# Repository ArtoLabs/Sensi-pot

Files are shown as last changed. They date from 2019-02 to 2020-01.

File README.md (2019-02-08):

#### Sensi-pot is open source hardware and software 
designed to help automate routine indoor garden processes such as lighting cycles, environment control, watering, and nutrient regulation. A prolific boom in the marijuana industry is taking place in Colorado, Oregon, and Washington states in the U.S. (and soon many other states) causing an increased demand for indoor gardening products. Especially in Colorado, where the winter is long and cold, most marijuana is grown indoors; necessitating equipment to help control and mimic the plant's native environment. This is especially needed for growing marijuana, which is very sensitive to heat and humidity (or lack thereof). However, most indoor gardening automation equipment is designed for big production facilities and is usually too expensive for the average grower. Sensi-pot provides electronics kits that can be easily assembled by anyone with a soldering iron, allowing the average user access to the same type of technology available to bigger growers at a fraction of the price.

# Sensi-Pot Indoor Environment Controller

This is the first Sensi-Pot open source automation device made for regulating the temperature and humidity of an enclosed space, including greenhouses. Marijuana grows best when the environment is kept at a perfect balance, and this device can maintain a perfect 55% humidity and 75 degrees fahrenheit, which is perfect for marijuana. The controller can be adjusted to regulate any temperature or level of humidity. At the heart of the device is the custom circuit board, which can be ordered using the open source Gerber files, or by [ordering through PCBway.com](https://www.pcbway.com/project/shareproject/Sensi_pot_Indoor_Environment_Controller.html) (see below for more info).

### Features

* Controls temperature to within 2 degrees.

* Controls humidity to within 5%.

* Wifi webserver shows the current temp and humidity as well as provides a manual way to active/deactivate any of the devices connected to it. You can also pause/unpause data logging from the web page as well as erase all data on the SD card.

* Data logging records the temperature and humidity with a timestamp to an SD card.

* Displays the current time, temperature and humidity on an LCD

### Hardware Specifications

* Designed using the open source PCB design and editing software, Kicad, so any changes you'd like to make to the circuit board can easily be done using the Kicad files available on Github.

* Uses the ATMEGA328P microcontroller, the same that can be found on any Arduino.

* The ATMEGA328P was programmed using the open source Arduino IDE software and uses some of the Arduino libraries in it's C++ code.

* Uses the ESP01 wifi module to serve a basic web page on the local network. To connect to a secured network the code must be modified slightly to include the SSID and the router password. The ATMEGA328P microcontroller communicates with the ESP01 using standard serial communication.

* Can technically control up to 8 devices and simply needs an 8 channel relay to do this. The pictures in this post show the controller connected to a 4 channel relay which is capable of controlling a heater, air conditioner, humidifier and dehumidifier. The other 4 devices can include lights and fans.

* Uses the DHT11 humidity and temperature sensor which can sense temperatures from 0 to 50 degrees Celsius (32 to 122 degrees Fahrenheit) +/- 2 degrees and can sense humidity from 20% to 80% +/- 5%. This can easily be replaced with no additional code with the DHT22 which has a temperature range of -40 to 125 (+/- 0.5) degrees Celsius and a humidity range of 0% to 100% (+/- 2 to 5 percent).

* Uses the MicroSD module to write logging data to any standard micro SD card. The ATMEGA328P communicates with the MicroSD module using the serial peripheral interface (SPI).

* Powered by the LM2596 adjustable buck converter which steps down any voltage between 9 and 34 volts to a regulated 5 volts used by the ATMEGA328P and it's peripheries. The voltage is further stepped down to 3.3 volts by the LM317 linear voltage regulator for use by the ESP01 wifi module. The Environment Controller consumes about 1.5 amps, with a peak current around 2 amps.

* Includes port access to programming pins via a 5 pin header that can be used to program the Environment Controller with an Arduino. Also includes access to the RX and TX pins of the ATMEGA328P so that a serial out connection can be made to a computer (mostly used for debugging).

### Software Specifications

There are actually two programs that were written to run on the Environment Controller; one for the ATMEGA328P microcontroller and one for the ESP01 wifi module which serves the webpage.

#### ATMEGA328P Software

* Programmed using the Arduino IDE and supporting libraries.

* Uses standard serial communication to transfer data between it and the ESP01 wifi module. All data is delineated by the "<" and ">" characters so that discrete amounts of data at any size can be transferred. This is very helpful as sending large amounts of data through a serial connection can be fraught with problems.

```
// Receives data from the ESP01 via serial connection
void recvESPData() {
    static boolean recvInProgress = false;
    static byte ndx = 0;
    char startMarker = '<'; // Delineate data
    char endMarker = '>';
    char rc;
    while (ESPserial.available() > 0 && newESPData == false) {
        rc = ESPserial.read();
        if (recvInProgress == true) {
            if (rc != endMarker) {
                receivedESPChars[ndx] = rc;
                ndx++;
                if (ndx >= numChars) {ndx = numChars – 1;} 
			// Step through one character at a time
            }
            else {
                receivedESPChars[ndx] = '\0'; // terminate the string
                recvInProgress = false;
                ndx = 0;
                newESPData = true;
            }
        }
        else if (rc == startMarker) {recvInProgress = true;}
    }
}
```

* Uses the Arduino `<SoftwareSerial.h>` library to communicate to the ESP01 since the RX and TX pins are still used for debugging.

* Uses the Arduino `<SD.h>` and `<SPI.h>` libraries to communicate with the MicroSD module for data logging.

```
myFile = SD.open("data.txt", FILE_WRITE); // Prepare SD card

…

    if (Tf > 74) {  //  If the temperature is greater than 74
      if (heaterActive) {
          heaterActive = false;
          logdevice =  cT + ":HE:0"; // cT is the timestamp, HE is code for heater
          lcd.setCursor(0, 1);
          lcd.print("Heat deactivated");
          if (myFile) {
            myFile.println(logdevice); // Log to SD card
          }
      }
      if ((Tf > 76) && (!acActive)){  //  If the temperature is greater than 76
          acActive = true;
          logdevice =  cT + ":AC:1";
          lcd.setCursor(0, 1);
          lcd.print("AC activated    ");
          if (myFile) {
            myFile.println(logdevice); // Log to SD card
          }
      }
    }
```
The example code block above shows how the data gets written to the SD card. Below shows how the data on the card is accessed and sent to the ESP01 to be displayed on the web page.

```
void getSDdata () { // Fetches the logging data from the SD card and prints it
                    // to the ESP01 via serial
    myFile = SD.open("/data.txt", FILE_READ);
    if(myFile) {
        ESPserial.print("<");
        while (myFile.available()) {
          ESPserial.write(myFile.read());
        }
        ESPserial.println(">");
        myFile.close();
    }
    else {
      lcd.setCursor(0, 1);
      lcd.print("Error reading SD"); 
    }
}
```
* Uses the `<LiquidCrystal.h>` library to display data on the LCD.

* Uses the `<SimpleDHT.h>` library to fetch temperature and humidity data from the sensor.

* A binary system was created to utilize the shift register. Since there are eight possible devices that can be controlled, all 8 outputs of the shift register are used. A binary number contains 8 digits, where a 1 indicates that a device is on, and a 0 indicates a devices is off. Binary math (xor) is used to add all the binary states of each device together to create one binary number that represents the state of all devices.

```
const byte relay1 = 0x80; //0b10000000    HUMIDIFIER      green
const byte relay2 = 0x40; //0b01000000    DE-HUMIDIFIER   red
const byte relay3 = 0x20; //0b00100000    HEATER          yellow
const byte relay4 = 0x10; //0b00010000    AC              green
const byte relay5 = 0x08; //0b00001000    FAN 1
const byte relay6 = 0x04; //0b00000100    FAN 2
const byte relay7 = 0x02; //0b00000010    FAN 3
const byte relay8 = 0x01; //0b00000001    FAN 4
void activateDevice () {
  state = allOff; 
  if (humidifierActive) { state = relay1; }
  if (dehumidifierActive) { state = state xor relay2; }
  if (heaterActive) { state = state xor relay3; }
  if (acActive) { state = state xor relay4; }
  state = allOn - state; // The shift register needs the opposite: On = 0, Off = 1
  writeReg(state);
}
```

#### ESP01 Software

* Programmed using the Arduino IDE and supporting libraries.

* Contains a small amount of CSS and HTML stored in `rawliteral` memory used to display the web page.

```
const char* FORM_HEADER = R"rawliteral(
<div id="side"><form id='theform' action='http://)rawliteral";

const char* FORM_MIDDLE = R"rawliteral(' method='POST'>
<a href='#' onClick="document.getElementById('ARG').value='2'; document.getElementById('theform').submit();">
<div class="btn">Get SD Data</div></a>
<a href='#' onClick="document.getElementById('ARG').value='1'; document.getElementById('theform').submit();">
<div class="btn">Delete SD Data</div></a>
)rawliteral";

const char* UNPAUSED = R"rawliteral(
<a href='#' onClick="document.getElementById('ARG').value='3'; document.getElementById('theform').submit();">
<div class="btn">Pause Logging</div></a>
)rawliteral";

const char* PAUSED = R"rawliteral(
<a href='#' onClick="document.getElementById('ARG').value='3'; document.getElementById('theform').submit();">
<div class="btn">Resume Logging</div></a>
)rawliteral";

const char* FORM_FOOTER = R"rawliteral(
<input type='hidden' name='ARG' id='ARG'>
<input type='hidden' name='ARG2' id='ARG2'>
</form></div>
)rawliteral";
```
* Uses the `<time.h>` and `<TimeLib.h>` libraries to fetch the current time from the Internet (time.nist.gov) and sets it local time by this. This is used to create the Unix timestamps for logging, and to convert Unix timestamps to human readable days, minutes, hours and the date. 

* The ESP01 libraries handle form submission on the web page, but a custom function was created to parse the data and commence the action.

```
void handleSubmit() {
  String Davalue;
  String dev;
  Davalue = server.arg("ARG");
  dev = server.arg("ARG2");
  if (Davalue == "1") {       // Delete all data on the SD card
    Serial.println("<2>");    // Returns a success code to the ATMEGA328P (only indicates code was received)
    time_t timer = time(nullptr);
    while (!Serial.available()) { 
      time_t now = time(nullptr);  // Every action has a 10 second timeout period
      if (now > timer + 10) {
        startPage();
        makeSideBar();
        makePageTop();
        server.sendContent("<div id='content'><h3>Could not delete data</h3></div>");
        makePageBottom();
        dataErr = true;
        break; 
      }
    }
    if (!dataErr) {
      startPage();
      makeSideBar();
      makePageTop();
      server.sendContent("<div id='content'><h3>SD card has been deleted</h3></div>");
      makePageBottom();
      dataErr = false;
    }
  }
  else if (Davalue == "2") {  // Retieves the logging data from the SD card and display it on the webpage
    Serial.print("<1>");      // Send the success code to the ATMEGA328P (only indicates code was received)
    waitForData = true;
    time_t timer = time(nullptr);  // 10 second timeout period
    while (!Serial.available()) { 
      time_t now = time(nullptr);
      if (now > timer + 10) {
        startPage();
        makeSideBar();
        makePageTop();
        server.sendContent("<div id='content'><h3>Could not get data</h3></div>");
        makePageBottom();
        waitForData == false;
        break; 
      }
    }
  }
  else if (Davalue == "3") {  // Pauses logging
    Serial.print("<5>");
    time_t timer = time(nullptr);   // 10 second timeout period
    while (!Serial.available()) {
      time_t now = time(nullptr);
      if (now > timer + 10) {
        startPage();
        makeSideBar();
        makePageTop();
        server.sendContent("<div id='content'><h3>Logging could not be paused</h3></div>");
        makePageBottom();
        break; 
      }
    }
  }
  else if (Davalue == "4") {  // Changes the on/off state of a device when the user clicks a button
    Serial.print("<D");
    Serial.print(dev);
    Serial.print(">");
    time_t timer = time(nullptr);
    while (!Serial.available()) {
      time_t now = time(nullptr);
      if (now > timer + 10) {
        startPage();
        makeSideBar();
        makePageTop();
        server.sendContent("<div id='content'><h3>Device could not be reached</h3></div>");
        makePageBottom();
        break; 
      }
    }
  }
  else {returnFail("Bad value");}
}
```

* The ESP01 is used by the ATMEGA328P to request the current timestamp each time data is logged.

```
      if (receivedChars[0] == '1') {  // The single digit code 1 requests the current time
                                      // This request is used for data logging
          time_t t = time(nullptr);
          int seconds = (int) t;
          char ds[10];
          itoa(seconds,ds,10);      // the time is sent as a UNIX timestamp
          Serial.print ("<");
          for(int i=0;i<10;i++) {
            Serial.print(ds[i]);    // Send the data back to ATMEGA328P
          }
          Serial.print (">");
      }
      else if (receivedChars[0] == '2') { // Code 2 requests the ESP01 sets it's own time to the current time
                                          // This request is used for displaying the time and date
          time_t t = time(nullptr);
          setTime(t);
          char buf[20];
          sprintf(buf,"%d-%02d-%02d %02d:%02d:%02d", year(), month(),
          day(), hour(), minute(), second());
          Serial.print ("<");
          for(int i=0;i<20;i++) {
            Serial.print(buf[i]);
          }
          Serial.print (">");
      }
```

### Assembling The Sensi-Pot Indoor Environment Controller

The circuit board has on it a lable for every part, so assembling and soldering should be very simple. A complete BOM (Bill of Materials) is included in the Github repository so ordering all the parts should also be relatively easy. A complete set of assembly instructions along with a "how-to" video will be created in the near future. 

#### [Order this circuit board from PCBway.com](https://www.pcbway.com/project/shareproject/Sensi_pot_Indoor_Environment_Controller.html)
Since Artolabs uses PCBway.com for it's circuit board production you can take advantage of PCBway's share program and simply order this circuit board without the need to submit the Gerber files! You [get 5 circuit boards for $5](https://www.pcbway.com/project/shareproject/Sensi_pot_Indoor_Environment_Controller.html) (plus about $8 shipping), and Artolabs gets a small commission too. 

ArtoLabs uses PCBway.com exclusively for small run production and prototyping. They provide outstanding customer service, and carefully review each order. It was surprising and comforting when they found some very small details I had overlooked and gave me a chance to correct my boards before manufacturing them.

#### Technology Stack

Sensi-Pot uses the Arduino open source library, Kicad open source PCB design software, and is written in C++.

#### Roadmap

This is obviously a working prototype. There are actually an incredible number of improvements planned for the Sensi-Pot Environment Controller, including an alarm circuit (for notifying when the temperature or humidity has gone out of control, perhaps due to a malfunctioning device), an LDR (Light Detecting Resistor) to enable the LCD and LEDs to power off when the grow area is in the "lights out" phase of the day, a soft power up circuit to prevent the shift register from activating when the Environment Controller is switched on, and too many more to mention. Sensi-Pot also has in the works a Soil Sensor Array to monitor the soil conditions of up to 10 plants per array, as well as many more automation devices.

#### Contact

Please contact Mike (Mike-A) on Discord
https://discord.gg/97GKVFC

#### Additional Resources
https://github.com/arduino/Arduino
https://github.com/KiCad

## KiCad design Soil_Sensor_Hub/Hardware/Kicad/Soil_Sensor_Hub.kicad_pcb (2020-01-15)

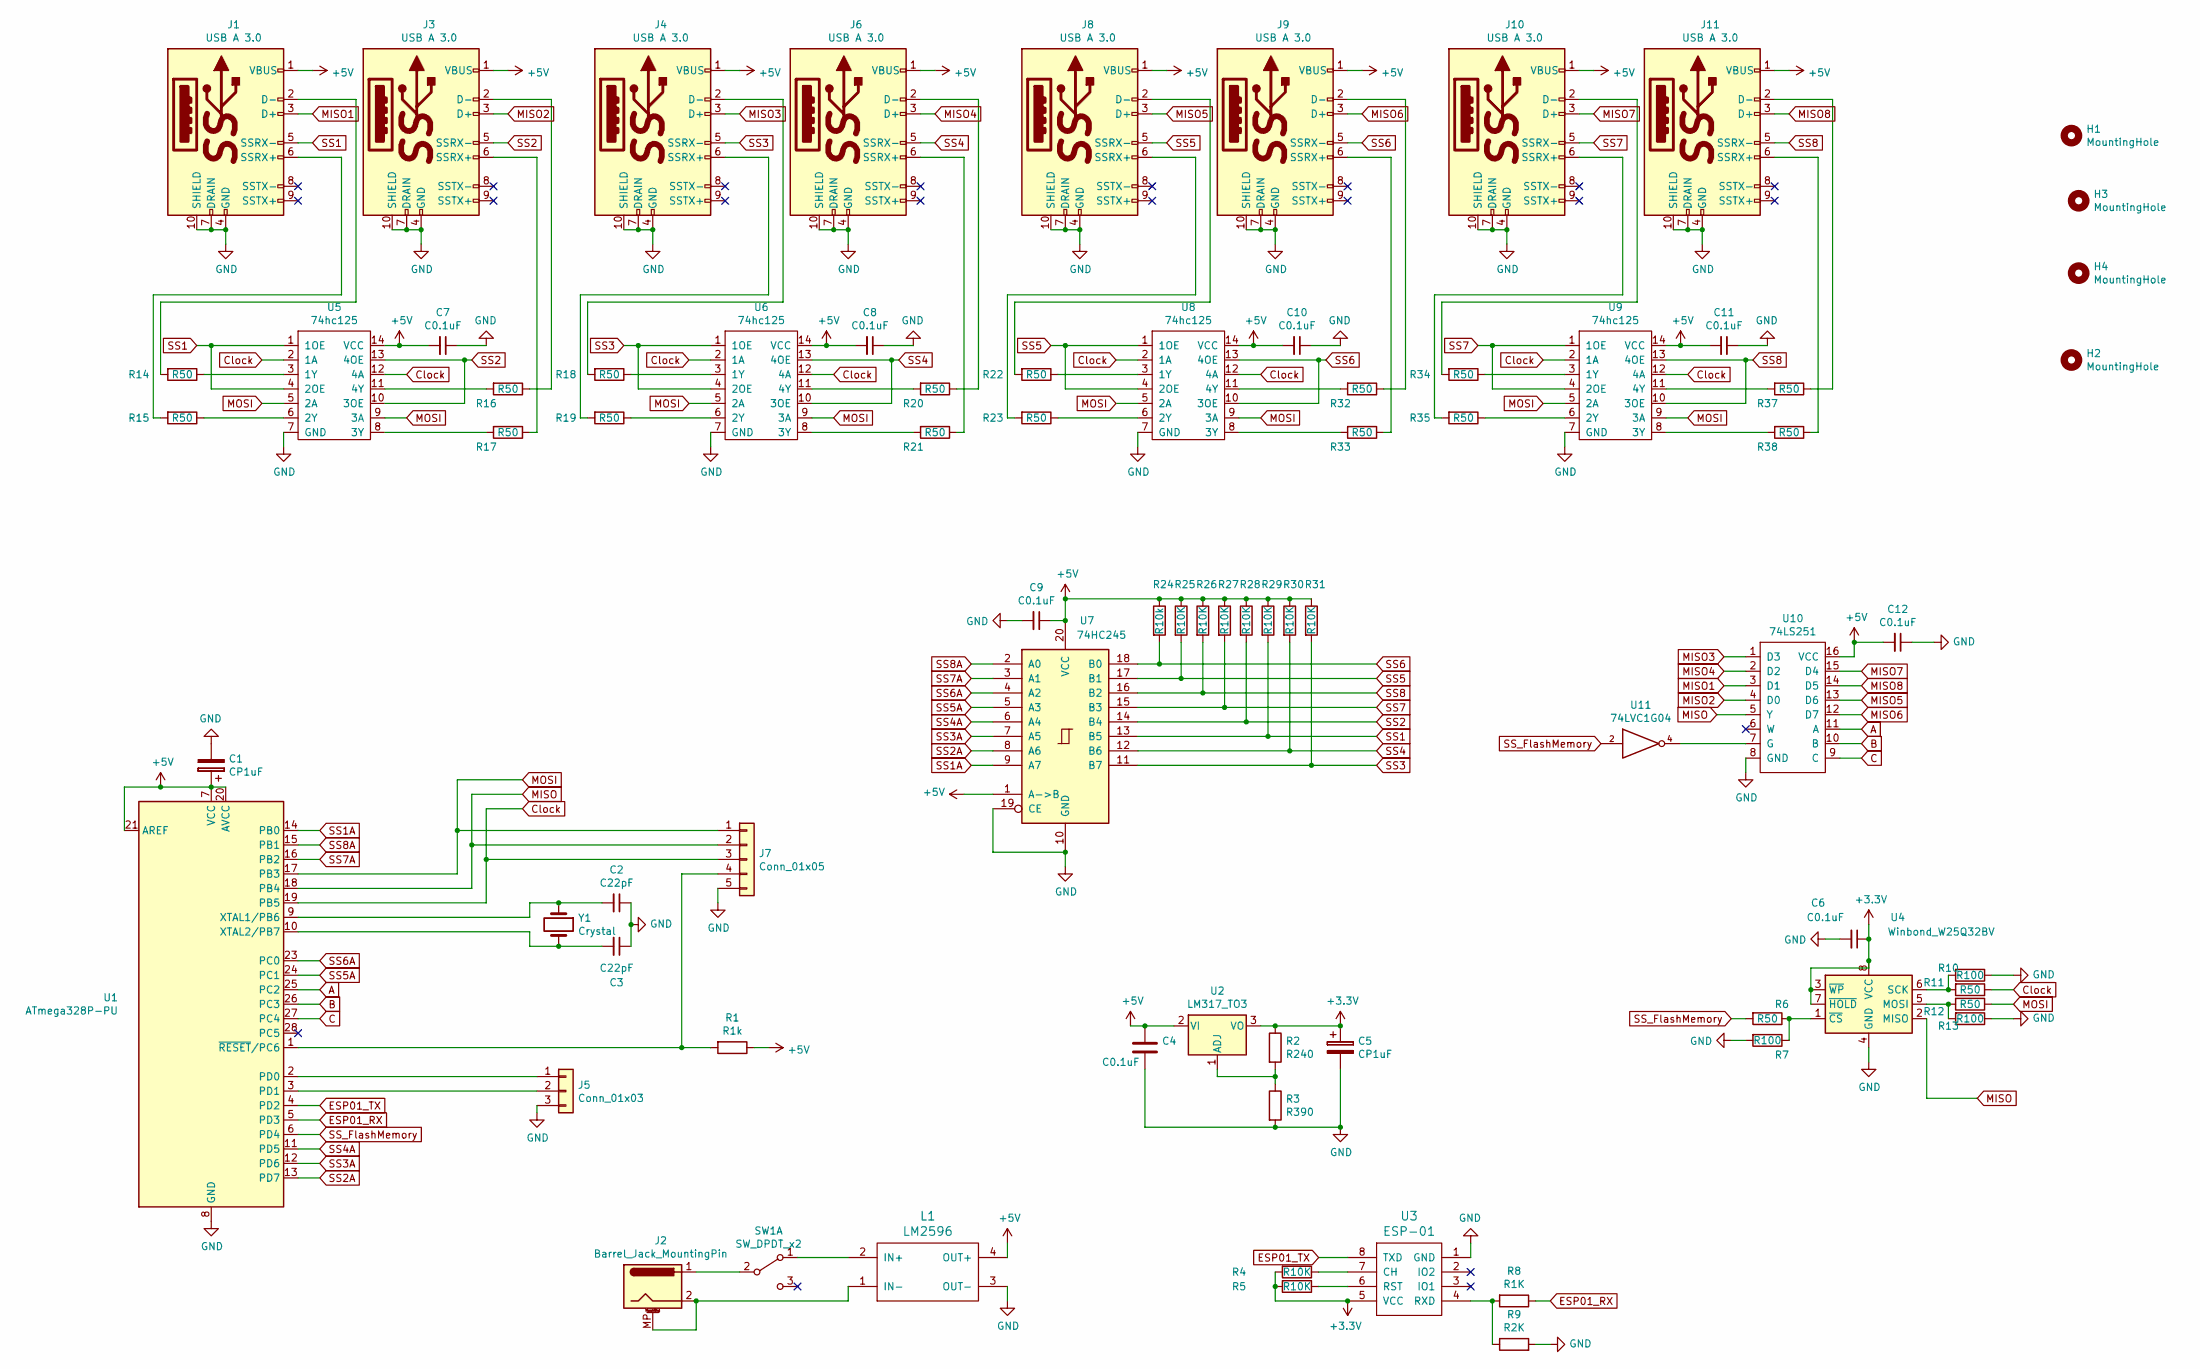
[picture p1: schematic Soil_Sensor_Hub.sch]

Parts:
C1, C5: CP1uF; CP_Radial_D4.0mm_P1.50mm_bigger_pads
C2, C3: C22pF; C_Disc_D3.0mm_W1.6mm_P2.50mm
C4, C6, C7, C8, C9, C10, C11, C12: C0.1uF; C_Disc_D3.0mm_W1.6mm_P2.50mm
H1, H2, H3, H4: MountingHole; MountingHole_3.2mm_M3
J1, J3, J4, J6, J8, J9, J10, J11: USB A 3.0; USB3_A_Molex_Edited
J2: Barrel_Jack_MountingPin; BarrelJack_Horizontal
J5: Conn_01x03; PinHeader_1x03_P2.54mm_Vertical
J7: Conn_01x05; PinHeader_1x05_P2.54mm_Vertical
L1: LM2596; LM2596_Module
R1: R1k; R_Axial_DIN0204_L3.6mm_D1.6mm_P7.62mm_Horizontal_bigger_pads
R2: R240; R_Axial_DIN0204_L3.6mm_D1.6mm_P7.62mm_Horizontal_bigger_pads
R3: R390; R_Axial_DIN0204_L3.6mm_D1.6mm_P7.62mm_Horizontal_bigger_pads
R4, R5, R25, R26, R27, R28, R29, R30, R31: R10K; R_Axial_DIN0204_L3.6mm_D1.6mm_P7.62mm_Horizontal_bigger_pads
R6, R11, R12, R14, R15, R16, R17, R18, R19, R20, R21, R22, R23, R32, R33, R34, R35, R37, R38: R50; R_Axial_DIN0204_L3.6mm_D1.6mm_P7.62mm_Horizontal_bigger_pads
R7, R10, R13: R100; R_Axial_DIN0204_L3.6mm_D1.6mm_P7.62mm_Horizontal_bigger_pads
R8: R1K; R_Axial_DIN0204_L3.6mm_D1.6mm_P7.62mm_Horizontal_bigger_pads
R9: R2K; R_Axial_DIN0204_L3.6mm_D1.6mm_P7.62mm_Horizontal_bigger_pads
R24: R10k; R_Axial_DIN0204_L3.6mm_D1.6mm_P7.62mm_Horizontal_bigger_pads
SW1: SW_DPDT_x2; PinHeader_1x03_P2.54mm_Vertical
U1: ATmega328P-PU; DIP-28_W7.62mm
U2: LM317_TO3; TO-220-3_Vertical
U3: ESP-01
U4: Winbond_W25Q32BV; SOIC-8_3.9x4.9mm_P1.27mm
U5, U6, U8, U9: 74hc125; DIP-14_W7.62mm
U7: 74HC245; DIP-20_W7.62mm
U10: 74LS251; DIP-16_W7.62mm
U11: 74LVC1G04; SOT-23-5_HandSoldering
Y1: Crystal; Crystal_HC18-U_Vertical

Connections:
+3V3: C5.1, C6.1, R2.1, R4.2, R5.2, U2.3 (VO), U3.5 (VCC), U4.3 (~WP), U4.7 (~HOLD), U4.8 (VCC)
+5V: C1.1, C4.1, C7.2, C8.2, C9.1, C10.2, C11.2, C12.2, J1.1 (VBUS), J3.1 (VBUS), J4.1 (VBUS), J6.1 (VBUS), J8.1 (VBUS), J9.1 (VBUS), J10.1 (VBUS), J11.1 (VBUS), L1.4 (OUT+), R1.1, R24.1, R25.1, R26.1, R27.1, R28.1, R29.1, R30.1, R31.1, U1.7 (VCC), U1.20 (AVCC), U1.21 (AREF), U2.2 (VI), U5.14 (VCC), U6.14 (VCC), U7.1 (A->B), U7.20 (VCC), U8.14 (VCC), U9.14 (VCC), U10.16 (VCC)
A: U1.25 (PC2), U10.11 (A)
B: U1.26 (PC3), U10.10 (B)
C: U1.27 (PC4), U10.9 (C)
Clock: J7.3, R11.1, U1.19 (PB5), U5.2 (1A), U5.12 (4A), U6.2 (1A), U6.12 (4A), U8.2 (1A), U8.12 (4A), U9.2 (1A), U9.12 (4A)
ESP01_RX: R8.1, U1.5 (PD3)
ESP01_TX: U1.4 (PD2), U3.8 (TXD)
GND: C1.2, C2.1, C3.1, C4.2, C5.2, C6.2, C7.1, C8.1, C9.2, C10.1, C11.1, C12.1, J1.4 (GND), J1.7 (DRAIN), J1.10 (SHIELD), J3.4 (GND), J3.7 (DRAIN), J3.10 (SHIELD), J4.4 (GND), J4.7 (DRAIN), J4.10 (SHIELD), J5.3, J6.4 (GND), J6.7 (DRAIN), J6.10 (SHIELD), J7.5, J8.4 (GND), J8.7 (DRAIN), J8.10 (SHIELD), J9.4 (GND), J9.7 (DRAIN), J9.10 (SHIELD), J10.4 (GND), J10.7 (DRAIN), J10.10 (SHIELD), J11.4 (GND), J11.7 (DRAIN), J11.10 (SHIELD), L1.3 (OUT-), R3.2, R7.2, R9.2, R10.1, R13.1, U1.8 (GND), U1.22 (GND), U3.1 (GND), U4.4 (GND), U5.7 (GND), U6.7 (GND), U7.10 (GND), U7.19 (CE), U8.7 (GND), U9.7 (GND), U10.8 (GND), U11.3 (GND)
MISO: J7.2, U1.18 (PB4), U4.2 (MISO), U10.5 (Y)
MISO1: J1.3 (D+), U10.3 (D1)
MISO2: J3.3 (D+), U10.4 (D0)
MISO3: J4.3 (D+), U10.1 (D3)
MISO4: J6.3 (D+), U10.2 (D2)
MISO5: J8.3 (D+), U10.13 (D6)
MISO6: J9.3 (D+), U10.12 (D7)
MISO7: J10.3 (D+), U10.15 (D4)
MISO8: J11.3 (D+), U10.14 (D5)
MOSI: J7.1, R12.1, U1.17 (PB3), U5.5 (2A), U5.9 (3A), U6.5 (2A), U6.9 (3A), U8.5 (2A), U8.9 (3A), U9.5 (2A), U9.9 (3A)
unnamed: C2.2, U1.9 (XTAL1/PB6), Y1.1
unnamed: C3.2, U1.10 (XTAL2/PB7), Y1.2
unnamed: J1.2 (D-), R14.2
unnamed: J1.6 (SSRX+), R15.2
unnamed: J2.1, SW1.2 (B)
unnamed: J2.2, J2.MP (MountPin), L1.1 (IN-)
unnamed: J3.2 (D-), R16.1
unnamed: J3.6 (SSRX+), R17.1
unnamed: J4.2 (D-), R18.2
unnamed: J4.6 (SSRX+), R19.2
unnamed: J5.1, U1.2 (PD0)
unnamed: J5.2, U1.3 (PD1)
unnamed: J6.2 (D-), R20.1
unnamed: J6.6 (SSRX+), R21.1
unnamed: J7.4, R1.2, U1.1 (~RESET~/PC6)
unnamed: J8.2 (D-), R22.2
unnamed: J8.6 (SSRX+), R23.2
unnamed: J9.2 (D-), R32.1
unnamed: J9.6 (SSRX+), R33.1
unnamed: J10.2 (D-), R34.2
unnamed: J10.6 (SSRX+), R35.2
unnamed: J11.2 (D-), R37.1
unnamed: J11.6 (SSRX+), R38.1
unnamed: L1.2 (IN+), SW1.1 (A)
unnamed: R2.2, R3.1, U2.1 (ADJ)
unnamed: R4.1, U3.7 (CH)
unnamed: R5.1, U3.6 (RST)
unnamed: R6.1, R7.1, U4.1 (~CS)
unnamed: R8.2, R9.1, U3.4 (RXD)
unnamed: R10.2, R11.2, U4.6 (SCK)
unnamed: R12.2, R13.2, U4.5 (MOSI)
unnamed: R14.1, U5.3 (1Y)
unnamed: R15.1, U5.6 (2Y)
unnamed: R16.2, U5.11 (4Y)
unnamed: R17.2, U5.8 (3Y)
unnamed: R18.1, U6.3 (1Y)
unnamed: R19.1, U6.6 (2Y)
unnamed: R20.2, U6.11 (4Y)
unnamed: R21.2, U6.8 (3Y)
unnamed: R22.1, U8.3 (1Y)
unnamed: R23.1, U8.6 (2Y)
unnamed: R32.2, U8.11 (4Y)
unnamed: R33.2, U8.8 (3Y)
unnamed: R34.1, U9.3 (1Y)
unnamed: R35.1, U9.6 (2Y)
unnamed: R37.2, U9.11 (4Y)
unnamed: R38.2, U9.8 (3Y)
unnamed: U10.7 (G), U11.4
SS1: J1.5 (SSRX-), R29.2, U5.1 (1OE), U5.4 (2OE), U7.13 (B5)
SS1A: U1.14 (PB0), U7.9 (A7)
SS2: J3.5 (SSRX-), R28.2, U5.10 (3OE), U5.13 (4OE), U7.14 (B4)
SS2A: U1.13 (PD7), U7.8 (A6)
SS3: J4.5 (SSRX-), R31.2, U6.1 (1OE), U6.4 (2OE), U7.11 (B7)
SS3A: U1.12 (PD6), U7.7 (A5)
SS4: J6.5 (SSRX-), R30.2, U6.10 (3OE), U6.13 (4OE), U7.12 (B6)
SS4A: U1.11 (PD5), U7.6 (A4)
SS5: J8.5 (SSRX-), R25.2, U7.17 (B1), U8.1 (1OE), U8.4 (2OE)
SS5A: U1.24 (PC1), U7.5 (A3)
SS6: J9.5 (SSRX-), R24.2, U7.18 (B0), U8.10 (3OE), U8.13 (4OE)
SS6A: U1.23 (PC0), U7.4 (A2)
SS7: J10.5 (SSRX-), R27.2, U7.15 (B3), U9.1 (1OE), U9.4 (2OE)
SS7A: U1.16 (PB2), U7.3 (A1)
SS8: J11.5 (SSRX-), R26.2, U7.16 (B2), U9.10 (3OE), U9.13 (4OE)
SS8A: U1.15 (PB1), U7.2 (A0)
SS_FlashMemory: R6.2, U1.6 (PD4), U11.2
VCC: U11.5 (VCC)

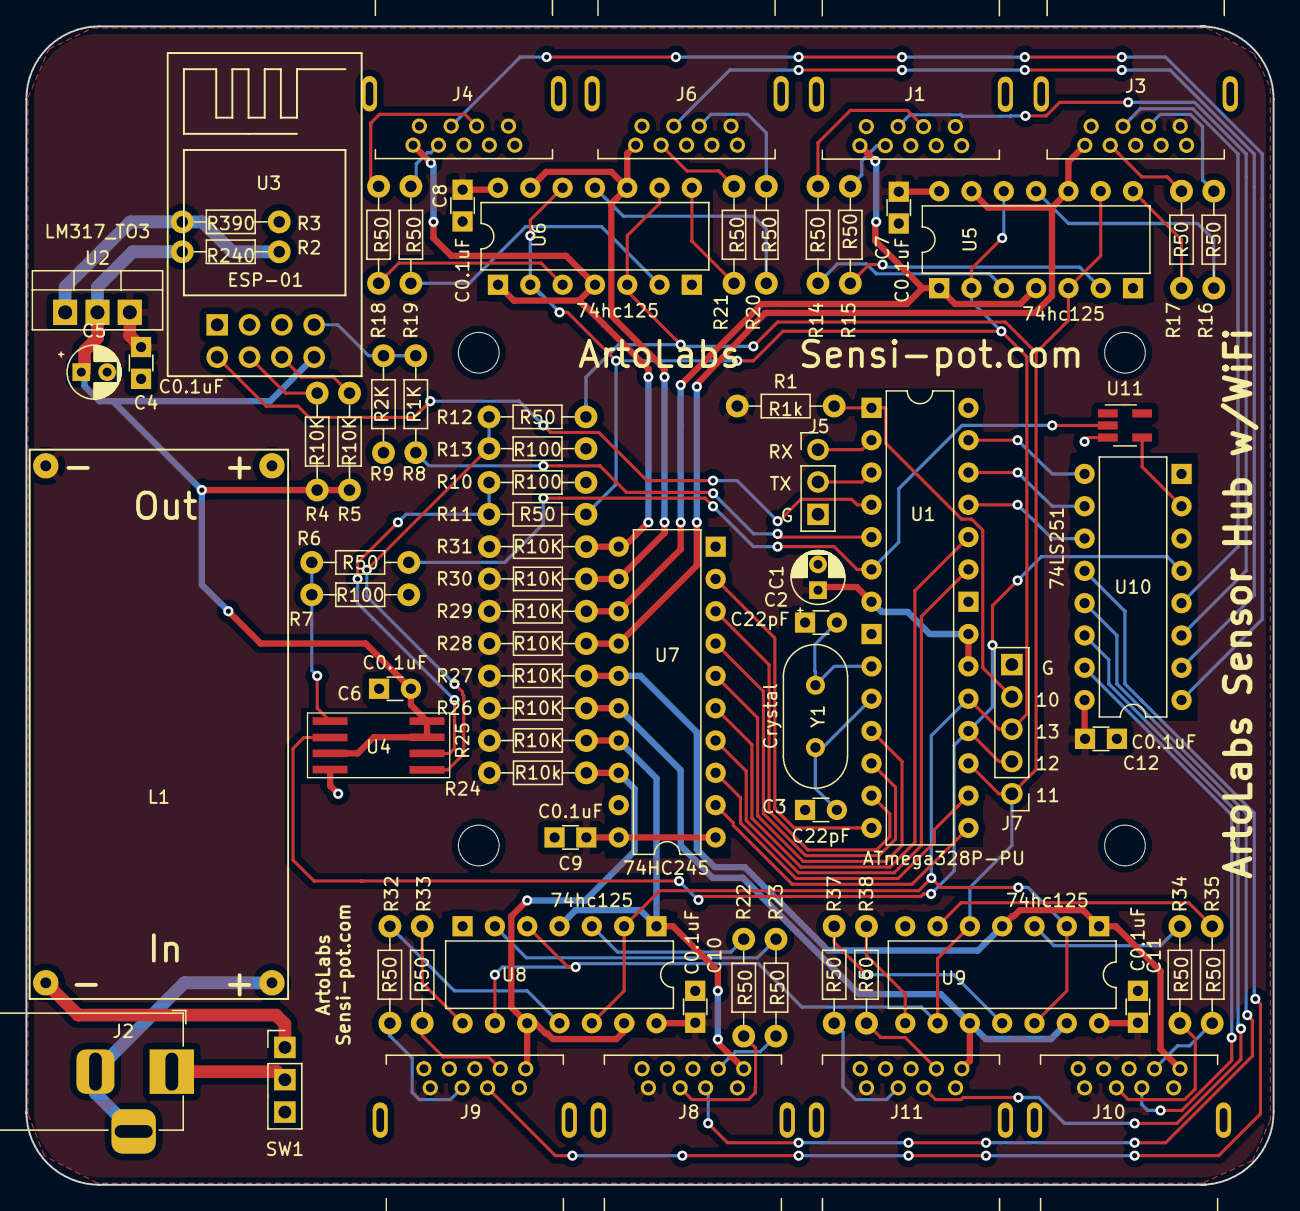
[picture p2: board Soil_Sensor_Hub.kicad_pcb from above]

Board: 2 copper layers, 98.0 x 91.1 mm, 78 parts (0 on the bottom side), 84 nets.

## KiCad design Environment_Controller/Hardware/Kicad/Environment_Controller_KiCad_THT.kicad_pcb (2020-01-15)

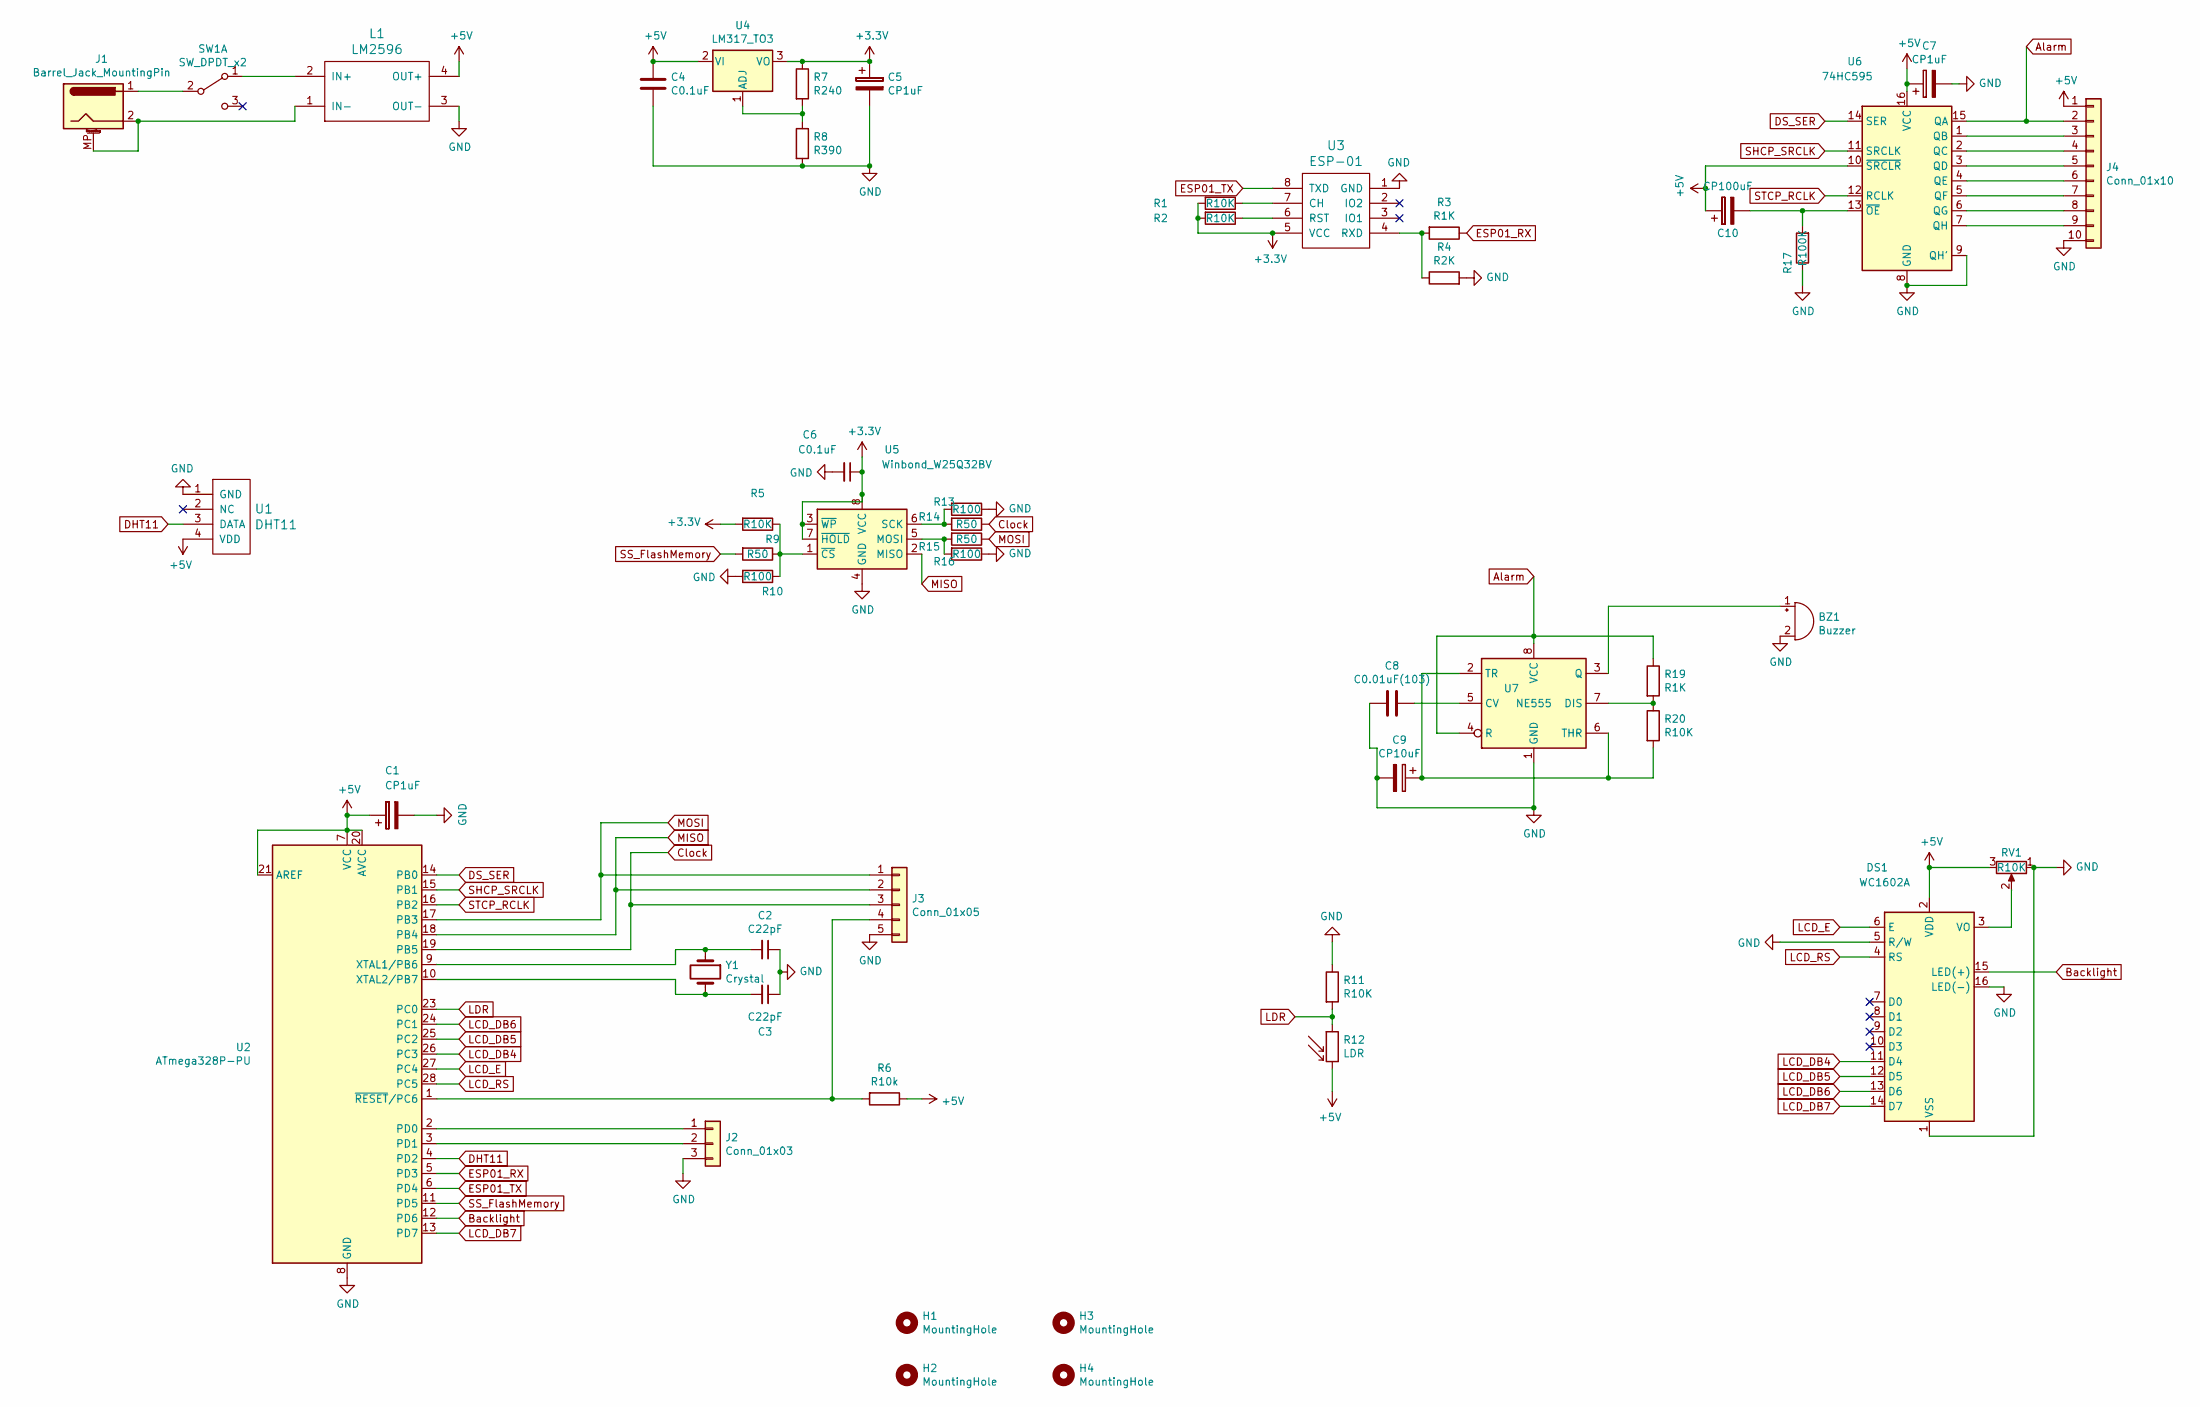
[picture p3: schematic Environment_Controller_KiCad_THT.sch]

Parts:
BZ1: Buzzer; Buzzer_12x9.5RM7.6
C1, C5, C7: CP1uF; CP_Radial_D4.0mm_P1.50mm_bigger_pads
C2, C3: C22pF; C_Disc_D3.0mm_W1.6mm_P2.50mm
C4, C6: C0.1uF; C_Disc_D3.0mm_W1.6mm_P2.50mm
C8: C0.01uF(103); C_Disc_D3.0mm_W1.6mm_P2.50mm
C9: CP10uF; CP_Radial_D4.0mm_P1.50mm_bigger_pads
C10: CP100uF; CP_Radial_D5.0mm_P2.50mm
DS1: WC1602A
H1, H2, H3, H4: MountingHole; MountingHole_3.2mm_M3
J1: Barrel_Jack_MountingPin; BarrelJack_Horizontal
J2: Conn_01x03; PinHeader_1x03_P2.54mm_Vertical
J3: Conn_01x05; PinHeader_1x05_P2.54mm_Vertical
J4: Conn_01x10; PinHeader_1x10_P2.54mm_Vertical
L1: LM2596; LM2596_Module
R1, R2, R5, R11, R20: R10K; R_Axial_DIN0204_L3.6mm_D1.6mm_P7.62mm_Horizontal_bigger_pads
R3, R19: R1K; R_Axial_DIN0204_L3.6mm_D1.6mm_P7.62mm_Horizontal_bigger_pads
R4: R2K; R_Axial_DIN0204_L3.6mm_D1.6mm_P7.62mm_Horizontal_bigger_pads
R6: R10k; R_Axial_DIN0204_L3.6mm_D1.6mm_P7.62mm_Horizontal_bigger_pads
R7: R240; R_Axial_DIN0204_L3.6mm_D1.6mm_P7.62mm_Horizontal_bigger_pads
R8: R390; R_Axial_DIN0204_L3.6mm_D1.6mm_P7.62mm_Horizontal_bigger_pads
R9, R14, R15: R50; R_Axial_DIN0204_L3.6mm_D1.6mm_P7.62mm_Horizontal_bigger_pads
R10, R13, R16: R100; R_Axial_DIN0204_L3.6mm_D1.6mm_P7.62mm_Horizontal_bigger_pads
R12: LDR; R_Axial_DIN0204_L3.6mm_D1.6mm_P1.90mm_Vertical
R17: R100K; R_Axial_DIN0204_L3.6mm_D1.6mm_P7.62mm_Horizontal_bigger_pads
RV1: R10K; Potentiometer_Bourns_3296W_Vertical
SW1: SW_DPDT_x2; PinHeader_1x03_P2.54mm_Vertical
U1: DHT11; PinHeader_1x04_P2.54mm_Vertical
U2: ATmega328P-PU; DIP-28_W7.62mm
U3: ESP-01
U4: LM317_TO3; TO-220-3_Vertical
U5: Winbond_W25Q32BV; SOIC-8_3.9x4.9mm_P1.27mm
U6: 74HC595; DIP-16_W7.62mm
U7: NE555; DIP-8_W7.62mm
Y1: Crystal; Crystal_HC18-U_Vertical

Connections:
+3V3: C5.1, C6.1, R1.2, R2.2, R5.2, R7.1, U3.5 (VCC), U4.3 (VO), U5.3 (~WP), U5.7 (~HOLD), U5.8 (VCC)
+5V: C1.1, C4.1, C7.1, C10.1, DS1.2 (VDD), J4.1, L1.4 (OUT+), R6.1, R12.2, RV1.3, U1.4 (VDD), U2.7 (VCC), U2.20 (AVCC), U2.21 (AREF), U4.2 (VI), U6.10 (~SRCLR), U6.16 (VCC)
Alarm: J4.2, R19.1, U6.15 (QA), U7.4 (R), U7.8 (VCC)
Backlight: DS1.15 (LED(+)), U2.12 (PD6)
Clock: J3.3, R14.1, U2.19 (PB5)
DHT11: U1.3 (DATA), U2.4 (PD2)
DS_SER: U2.14 (PB0), U6.14 (SER)
ESP01_RX: R3.1, U2.5 (PD3)
ESP01_TX: U2.6 (PD4), U3.8 (TXD)
GND: BZ1.2 (+), C1.2, C2.1, C3.1, C4.2, C5.2, C6.2, C7.2, C8.2, C9.2, DS1.1 (VSS), DS1.5 (R/W), DS1.16 (LED(-)), J2.3, J3.5, J4.10, L1.3 (OUT-), R4.2, R8.2, R10.2, R11.1, R13.1, R16.1, R17.1, RV1.1, U1.1 (GND), U2.8 (GND), U2.22 (GND), U3.1 (GND), U5.4 (GND), U6.8 (GND), U6.9 (QH'), U7.1 (GND)
LCD_DB4: DS1.11 (D4), U2.26 (PC3)
LCD_DB5: DS1.12 (D5), U2.25 (PC2)
LCD_DB6: DS1.13 (D6), U2.24 (PC1)
LCD_DB7: DS1.14 (D7), U2.13 (PD7)
LCD_E: DS1.6 (E), U2.27 (PC4)
LCD_RS: DS1.4 (RS), U2.28 (PC5)
LDR: R11.2, R12.1, U2.23 (PC0)
MISO: J3.2, U2.18 (PB4), U5.2 (MISO)
MOSI: J3.1, R15.1, U2.17 (PB3)
unnamed: BZ1.1 (-), U7.3 (Q)
unnamed: C2.2, U2.9 (XTAL1/PB6), Y1.1
unnamed: C3.2, U2.10 (XTAL2/PB7), Y1.2
unnamed: C8.1, U7.5 (CV)
unnamed: C9.1, R20.2, U7.2 (TR), U7.6 (THR)
unnamed: C10.2, R17.2, U6.13 (~OE)
unnamed: DS1.3 (VO), RV1.2
unnamed: J1.1, SW1.2 (B)
unnamed: J1.2, J1.MP (MountPin), L1.1 (IN-)
unnamed: J2.1, U2.2 (PD0)
unnamed: J2.2, U2.3 (PD1)
unnamed: J3.4, R6.2, U2.1 (~RESET~/PC6)
unnamed: J4.3, U6.1 (QB)
unnamed: J4.4, U6.2 (QC)
unnamed: J4.5, U6.3 (QD)
unnamed: J4.6, U6.4 (QE)
unnamed: J4.7, U6.5 (QF)
unnamed: J4.8, U6.6 (QG)
unnamed: J4.9, U6.7 (QH)
unnamed: L1.2 (IN+), SW1.1 (A)
unnamed: R1.1, U3.7 (CH)
unnamed: R2.1, U3.6 (RST)
unnamed: R3.2, R4.1, U3.4 (RXD)
unnamed: R7.2, R8.1, U4.1 (ADJ)
unnamed: R5.1, R9.1, R10.1, U5.1 (~CS)
unnamed: R13.2, R14.2, U5.6 (SCK)
unnamed: R15.2, R16.2, U5.5 (MOSI)
unnamed: R19.2, R20.1, U7.7 (DIS)
SHCP_SRCLK: U2.15 (PB1), U6.11 (SRCLK)
SS_FlashMemory: R9.2, U2.11 (PD5)
STCP_RCLK: U2.16 (PB2), U6.12 (RCLK)

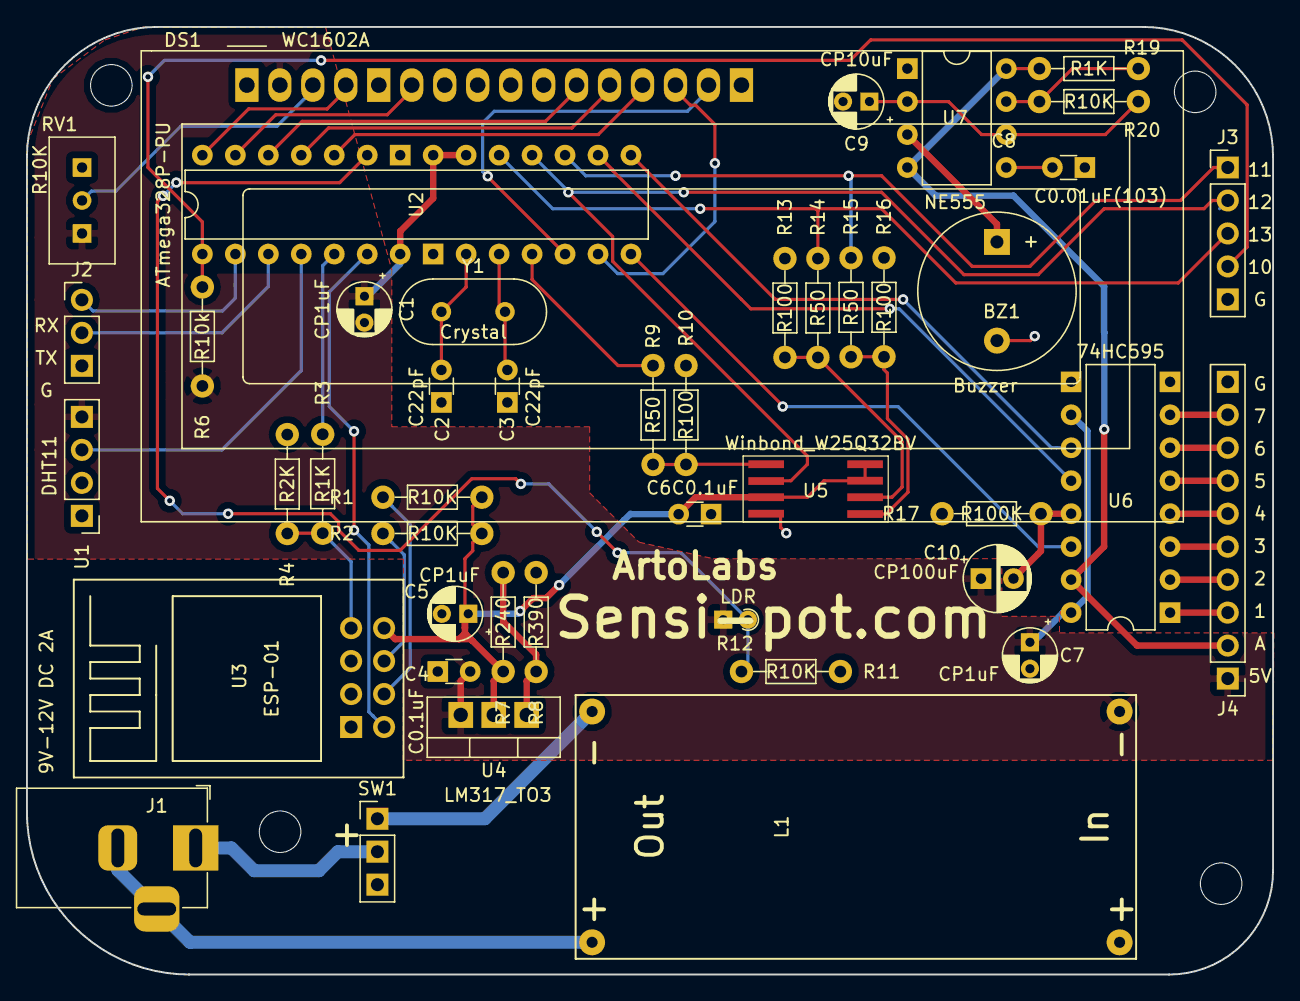
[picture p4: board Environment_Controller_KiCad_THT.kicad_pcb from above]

Board: 2 copper layers, 96.0 x 73.0 mm, 49 parts (0 on the bottom side), 50 nets.

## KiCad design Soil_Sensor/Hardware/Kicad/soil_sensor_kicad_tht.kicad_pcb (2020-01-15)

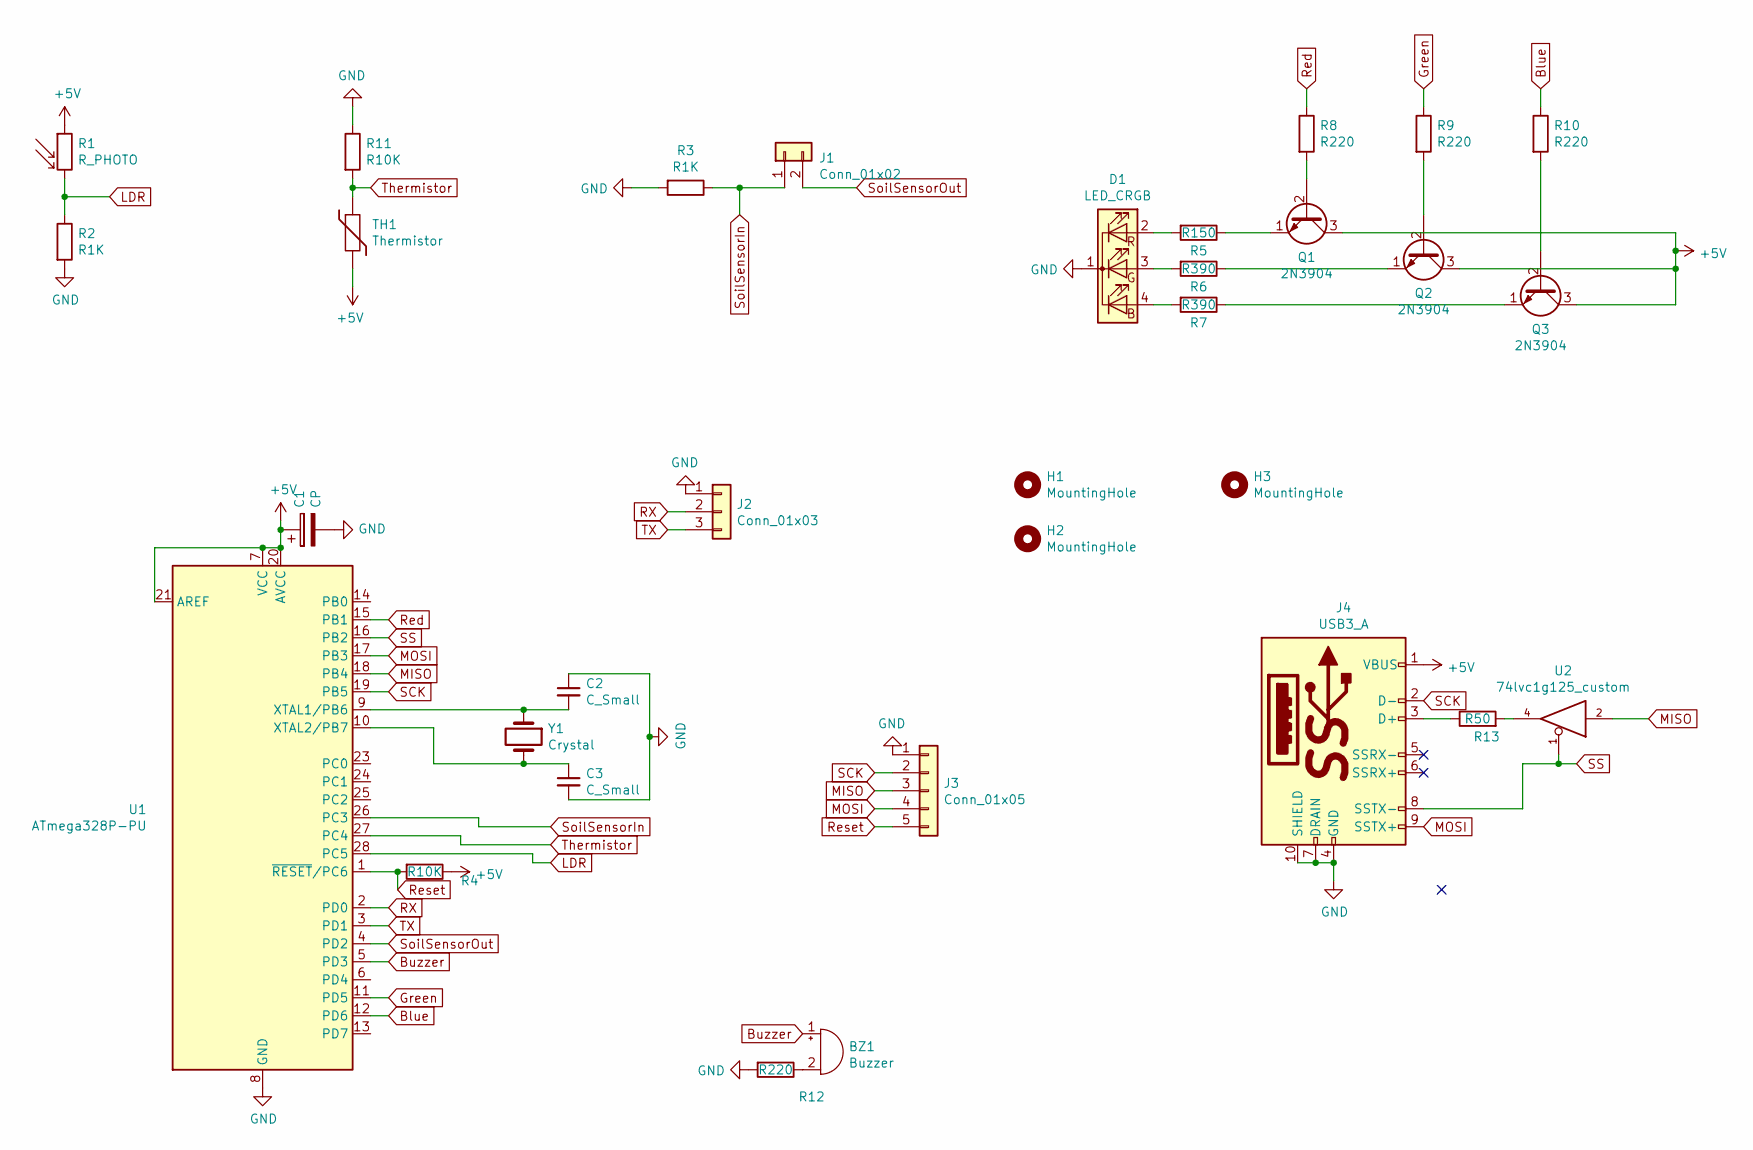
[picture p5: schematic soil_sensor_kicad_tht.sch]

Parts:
BZ1: Buzzer; Buzzer_12x9.5RM7.6
C1: CP; CP_Radial_D4.0mm_P1.50mm_bigger_pads
C2, C3: C_Small; C_Disc_D3.0mm_W1.6mm_P2.50mm
D1: LED_CRGB; LED_D5.0mm-4_RGB_Common_Cathode_2
H1, H2, H3: MountingHole; MountingHole_3.2mm_M3
J1: Conn_01x02; PinHeader_1x02_P2.54mm_Vertical
J2: Conn_01x03; PinHeader_1x03_P2.54mm_Vertical
J3: Conn_01x05; PinHeader_1x05_P2.54mm_Vertical
J4: USB3_A; USB3_A_Molex_Edited
Q1, Q2, Q3: 2N3904; TO-92_Inline_bigger_pads
R1: R_PHOTO; R_Axial_DIN0204_L3.6mm_D1.6mm_P1.90mm_Vertical
R2, R3: R1K; R_Axial_DIN0204_L3.6mm_D1.6mm_P7.62mm_Horizontal_bigger_pad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
R4, R11: R10K; R_Axial_DIN0204_L3.6mm_D1.6mm_P7.62mm_Horizontal_bigger_pad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
R5: R150; R_Axial_DIN0204_L3.6mm_D1.6mm_P7.62mm_Horizontal_bigger_pad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
R6, R7: R390; R_Axial_DIN0204_L3.6mm_D1.6mm_P7.62mm_Horizontal_bigger_pad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
R8, R9, R10, R12: R220; R_Axial_DIN0204_L3.6mm_D1.6mm_P7.62mm_Horizontal_bigger_pad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
R13: R50; R_Axial_DIN0204_L3.6mm_D1.6mm_P7.62mm_Horizontal_bigger_pad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
TH1: Thermistor; R_Axial_DIN0204_L3.6mm_D1.6mm_P1.90mm_Vertical
U1: ATmega328P-PU; DIP-28_W7.62mm
U2: 74lvc1g125_custom; SOT-23-5_HandSoldering
Y1: Crystal; Crystal_HC18-U_Vertical

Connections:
+5V: C1.1, J4.1 (VBUS), Q1.3 (C), Q2.3 (C), Q3.3 (C), R1.1, R4.1, TH1.2, U1.7 (VCC), U1.20 (AVCC), U1.21 (AREF), U2.5 (VCC)
Blue: R10.1, U1.12 (PD6)
Buzzer: BZ1.1 (-), U1.5 (PD3)
GND: C1.2, C2.1, C3.2, D1.1 (K), J2.1, J3.1, J4.4 (GND), J4.7 (DRAIN), J4.10 (SHIELD), R2.2, R3.2, R11.1, R12.2, U1.8 (GND), U1.22 (GND), U2.3 (GND)
Green: R9.1, U1.11 (PD5)
LDR: R1.2, R2.1, U1.28 (PC5)
MISO: J3.3, U1.18 (PB4), U2.2
MOSI: J3.4, J4.9 (SSTX+), U1.17 (PB3)
unnamed: BZ1.2 (+), R12.1
unnamed: C2.2, U1.9 (XTAL1/PB6), Y1.1
unnamed: C3.1, U1.10 (XTAL2/PB7), Y1.2
unnamed: D1.2 (RA), R5.2
unnamed: D1.3 (GA), R6.2
unnamed: D1.4 (BA), R7.2
unnamed: J4.3 (D+), R13.1
unnamed: Q1.1 (E), R5.1
unnamed: Q1.2 (B), R8.2
unnamed: Q2.1 (E), R6.1
unnamed: Q2.2 (B), R9.2
unnamed: Q3.1 (E), R7.1
unnamed: Q3.2 (B), R10.2
unnamed: R13.2, U2.4
RX: J2.2, U1.2 (PD0)
Red: R8.1, U1.15 (PB1)
Reset: J3.5, R4.2, U1.1 (~RESET~/PC6)
SCK: J3.2, J4.2 (D-), U1.19 (PB5)
SS: J4.8 (SSTX-), U1.16 (PB2), U2.1
SoilSensorIn: J1.1, R3.1, U1.26 (PC3)
SoilSensorOut: J1.2, U1.4 (PD2)
TX: J2.3, U1.3 (PD1)
Thermistor: R11.2, TH1.1, U1.27 (PC4)

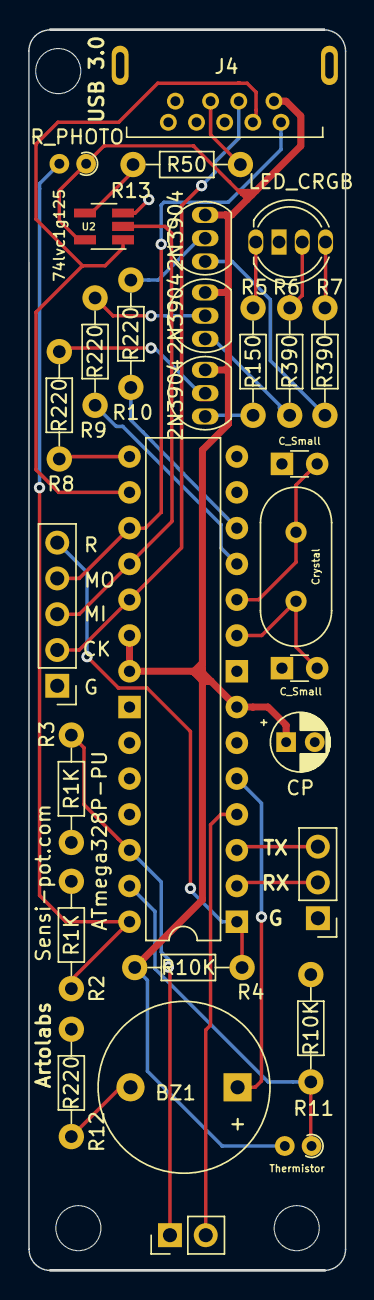
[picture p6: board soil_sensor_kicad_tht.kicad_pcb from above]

Board: 2 copper layers, 22.5 x 88.1 mm, 32 parts (0 on the bottom side), 31 nets.

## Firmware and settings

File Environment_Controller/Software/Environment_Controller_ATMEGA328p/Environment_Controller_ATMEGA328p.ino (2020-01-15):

#include <SimpleDHT.h>
#include <SoftwareSerial.h>
#include <SPI.h>
#include<SPIMemory.h>
#include <LiquidCrystal.h>
#include <Time.h>
#define RX 4  // Used to communicate with ESP-01 via serial
#define TX 3
#define pinDHT11 2
#define pinLDR A0
#define LOG_DATA_SIZE 18 // Unix timestamp (10 digits) + : (1 digit) humidity (2 digits) + temp (2 digits) + light (2 digits)
#define CS_PIN 5
#define backlight 6
// These are defined for the 74hc595 shift register
#define dataPin 8 // SER orange wire DS Data Pin 14 
#define latchPin 10 // SRCLK blue wire STCP Latch Pin 11 (Output Clock / Storage register clock pin)
#define clockPin 9 // RCLK yellow wire SHCP Clock Pin 12 (Input Clock / Shift register clock pin)
#define SETTINGS_MEMORY_ADDRESS 0x1F3000
#define SETTINGS_MEMORY_SIZE 256  // bytes
#define PASSWORD_SIZE 25
#define SSID_SIZE 25

//   USED TO DEBUG MEMORY PROBLEMS
//   REPORTS AVAILABLE MEMORY LEFT IN THE HEAP
#ifdef __arm__
// should use uinstd.h to define sbrk but Due causes a conflict
extern "C" char* sbrk(int incr);
#else  // __ARM__
extern char *__brkval;
#endif  // __arm__
int freeMemory() {
  char top;
#ifdef __arm__
  return &top - reinterpret_cast<char*>(sbrk(0));
#elif defined(CORE_TEENSY) || (ARDUINO > 103 && ARDUINO != 151)
  return &top - __brkval;
#else  // __arm__
  return __brkval ? &top - __brkval : &top - __malloc_heap_start;
#endif  // __arm__
}

const byte relay1 = 0x80; //0b10000000    HUMIDIFIER      green
const byte relay2 = 0x40; //0b01000000    DE-HUMIDIFIER   red
const byte relay3 = 0x20; //0b00100000    HEATER          yellow
const byte relay4 = 0x10; //0b00010000    AC              green
const byte relay5 = 0x08; //0b00001000    FAN 1
const byte relay6 = 0x04; //0b00000100    FAN 2
const byte relay7 = 0x02; //0b00000010    FAN 3
const byte relay8 = 0x01; //0b00000001    ALARM
const byte allOff = 0x00;
const byte allOn = 0xFF;
uint32_t lastKnownAddr;
char logData[LOG_DATA_SIZE];
char password[PASSWORD_SIZE];
char ssid[SSID_SIZE];
char timezone[4];
char loginterval[8];
char tempTarget[3];
char humTarget[3];
char almsettings[5];
char timer1hourON[3];
char timer1minuteON[3];
char timer2hourON[3];
char timer2minuteON[3];
char timer3hourON[3];
char timer3minuteON[3];
char timer1hourOFF[3];
char timer1minuteOFF[3];
char timer2hourOFF[3];
char timer2minuteOFF[3];
char timer3hourOFF[3];
char timer3minuteOFF[3];
unsigned long loggingInterval = 300000;  // log every 5 minutes
unsigned long sensorInterval = 15000;  // log every 5 seconds
unsigned long loggingTimer = 0;
unsigned long sensorTimer = 0;
byte state;
boolean humidifierActive = false, dehumidifierActive = false, heaterActive = false, acActive = false, fan1Active = false, fan2Active = false, fan3Active = false;
float Tf = 0;
float ldrPercentage = 0;
byte temperature = 0;
byte humidity = 0;
const byte numChars = 32;
char receivedESPChars[numChars]; // an array to store the received data
char receivedChars[numChars]; // an array to store the received ESP01 data
boolean newESPData = false, newData = false, recvInProgress = false, booting = true, waitForTimestamp = false, pauseLogging = false, alarmOn = false, wificonnected = false;
boolean firsttime = true;
boolean humidityHighAlarm = false, humidityLowAlarm = false, tempHighAlarm = false, tempLowAlarm = false;
boolean humidityHighTriggered = false, humidityLowTriggered = false, tempHighTriggered = false, tempLowTriggered = false;
unsigned long humidityHighTimer = 0;
unsigned long humidityLowTimer = 0;
unsigned long tempHighTimer = 0;
unsigned long tempLowTimer = 0;
const long alarmWaitPeriod = 1200000; // wait 20 minutes before triggering alarm
short int targetTemp = 75;
const int degreesOfForgiveness = 2;
short int degreesOfAlarm = 10;
short int targetHum = 55;
const int percentageOfForgiveness = 1;
short int percentageOfAlarm = 10;

// Function prototypes
bool checkLDR();
void activateDevice();
void writeReg(byte);
void formatData();
void activateDeviceTimer();
void requestHumTemp();
void logDataToMemory();
boolean logTimer();
boolean sensorRequestTimer();
void printLogDataBuffer();
void recvESPData();
void printChipStats(boolean);
void formatValue(char*, char*, size_t);
void getSettings(boolean);
void saveSettings();
void printDataToLog();
void printLog(boolean);
boolean endOfData(uint32_t);
void recvData();
void eraseLog();
void processESPData();
void processNewData();
String makeInfoString (char);


// Pin assignment for the LCD
//const int rs = 19, en = 18, d4 = 17, d5 = 15, d6 = 14, d7 = 6;
//LiquidCrystal lcd(rs, en, d4, d5, d6, d7);
LiquidCrystal lcd(19, 18, 17, 16, 15, 7);
SimpleDHT11 dht11;
SoftwareSerial ESPserial(RX, TX);
SPIFlash flash(CS_PIN);


void setup() {
  pinMode(dataPin, OUTPUT);
  pinMode(latchPin, OUTPUT);
  pinMode(clockPin, OUTPUT);
  pinMode(backlight, OUTPUT);
  writeReg(allOn); // Turn all devices off: shift regisiter is inverting
  activateDevice();
  if (checkLDR()) { digitalWrite(backlight, LOW); }
  else { digitalWrite(backlight, HIGH); }
  ESPserial.begin(9600);
  Serial.begin(115200); // Used for debugging
  lcd.begin(16, 2);
  lcd.setCursor(0, 0);
  lcd.print(F("Starting up!"));
  Serial.println("Starting up!");
  delay(1000);
  flash.begin();
  flash.setClock(1000); // A slow 1Khz to prevent reflections and distortions in the voltage dividers 
  Serial.print(F("Free bytes: "));
  Serial.println(freeMemory());
}


// Main loop
void loop() {
  if (checkLDR()) { digitalWrite(backlight, LOW); }
  else { digitalWrite(backlight, HIGH); }
  if (sensorRequestTimer()){
    ESPserial.print(F("<1>"));
    waitForTimestamp = true;
    activateDeviceTimer();
  }
  if (newESPData) {
    processESPData();
  }
  else if (ESPserial.available()) {
    recvESPData(); 
  }
  if (newData) {
    processNewData();
  }
  else if ((Serial.available()) && (recvInProgress == false)){
    recvData();
  }
}


bool checkLDR() {
  int sensorValue = analogRead(pinLDR);
  ldrPercentage = ((float)sensorValue / 1023) * 100;
  if (sensorValue < 200) { return true; }
  else { return false; }
}


// Changes the binary value for the shift register
void activateDevice() {
  state = allOff; 
  if (humidifierActive) { state = relay1; }
  if (dehumidifierActive) { state = state xor relay2; }
  if (heaterActive) { state = state xor relay3; }
  if (acActive) { state = state xor relay4; }
  if (fan1Active) { state = state xor relay5; }
  if (fan2Active) { state = state xor relay6; }
  if (fan3Active) { state = state xor relay7; }
  if (!(alarmOn)) { state = state xor relay8; }
  state = allOn - state; // The shift register needs the opposite: On = 0, Off = 1
  writeReg(state);
}


void writeReg(byte value) {
  digitalWrite(latchPin, LOW);    // Pulls the shift register latch low
  for(int i = 0; i < 8; i++){  // Repeat 8 times (once for each bit)
    int bit = value & B10000000; // Use a "bitmask" to select only the eighth bit
    if(bit == 128) {  digitalWrite(dataPin, HIGH); } //if bit 8 is a 1, set our data pin high
    else{ digitalWrite(dataPin, LOW); } //if bit 8 is a 0, set the data pin low
    digitalWrite(clockPin, HIGH);                // The next three lines pulse the clock
    delay(1);
    digitalWrite(clockPin, LOW);
    value = value << 1;          // Move the number up one bit value
  }
  digitalWrite(latchPin, HIGH);  // Pulls the latch high, to display the data
}


void formatData() {
  memset(logData, 0, sizeof(logData));
  logData[0] = '\0';
  strcat(logData, receivedESPChars); // this is the timestamp
  strcat(logData, ":");
  // Parse humidity into char array
  char humc[3];
  sprintf(humc, "%02d", (int)humidity);
  strcat(logData, humc);
  // Parse temperature into char array
  int tem = int(Tf);
  char temc[3];
  sprintf(temc, "%02d", (int)Tf);
  strcat(logData, temc);
  // Parse light sensor into char array
  int ldrPer = ldrPercentage;
  char ldrc[3];
  sprintf(ldrc, "%02d", ldrPer);
  strcat(logData, ldrc);
}


void activateDeviceTimer() {
  lcd.setCursor(0, 1);
  if ((hour() == atoi(timer1hourON)) && (minute() == atoi(timer1minuteON))) { fan1Active = true; }
  if ((hour() == atoi(timer2hourON)) && (minute() == atoi(timer2minuteON))) { fan2Active = true; }
  if ((hour() == atoi(timer3hourON)) && (minute() == atoi(timer3minuteON))) { fan3Active = true; }
  if ((hour() == atoi(timer1hourOFF)) && (minute() == atoi(timer1minuteOFF))) { fan1Active = false; }
  if ((hour() == atoi(timer2hourOFF)) && (minute() == atoi(timer2minuteOFF))) { fan2Active = false; }
  if ((hour() == atoi(timer3hourOFF)) && (minute() == atoi(timer3minuteOFF))) { fan3Active = false; }
  activateDevice();
}


void requestHumTemp() {  // The DHT11 is polled to find the temp and humidity
  int err = SimpleDHTErrSuccess;
  if ((err = dht11.read(pinDHT11, &temperature, &humidity, NULL)) != SimpleDHTErrSuccess) {
    // If the DHT11 encounters an error print it to the LCD
    lcd.clear();
    lcd.print(F("DHT11 error:    "));
    lcd.setCursor(0, 1);
    lcd.print(err);   
    return;
  }
  Tf = ((int)temperature * 9.0)/ 5.0 + 32.0;  // Convert temperature to fahrenheit
  if ((int)Tf > targetTemp + degreesOfForgiveness) {
    tempLowTriggered = false;
    heaterActive = false;
    acActive = true;
    if (((int)Tf >= targetTemp + degreesOfAlarm) && !(tempHighTriggered)) {
      tempHighTimer = millis();
      tempHighTriggered = true;
      Serial.println(F("High temp alarm timer triggered"));
    }
  }
  if ((int)Tf < targetTemp - degreesOfForgiveness){
    tempHighTriggered = false;
    acActive = false; 
    heaterActive = true;
    if (((int)Tf <= targetTemp - degreesOfAlarm) && !(tempLowTriggered)) { 
      tempLowTimer = millis();
      tempLowTriggered = true;
      Serial.println(F("Low temp alarm timer triggered"));
    }
  }
  if (((int)Tf <= targetTemp + degreesOfForgiveness) && ((int)Tf >= targetTemp - degreesOfForgiveness)) {
    tempHighTriggered = false;
    tempLowTriggered = false;
    if (((int)Tf == targetTemp) {
      acActive = false;
      heaterActive = false;
    }
  }
  if ((int)humidity > targetHum + percentageOfForgiveness) {
    humidityLowTriggered = false;
    humidifierActive = false;
    dehumidifierActive = true;
    if (((int)humidity >= targetHum + percentageOfAlarm) && !(humidityHighTriggered)) {
      humidityHighTimer = millis();
      humidityHighTriggered = true;
      Serial.println(F("High humidity alarm timer triggered"));
    }
  }
  if ((int)humidity < targetHum - percentageOfForgiveness) {
    humidityHighTriggered = false;
    dehumidifierActive = false;
    humidifierActive = true;
    if (((int)humidity <= targetHum - percentageOfAlarm) && !(humidityLowTriggered)) {
      humidityLowTimer = millis();
      humidityLowTriggered = true;
      Serial.println(F("Low humidity alarm timer triggered"));
    }
  }
  if (((int)humidity <= targetHum + percentageOfForgiveness) && ((int)humidity >= targetHum - percentageOfForgiveness))  {
    humidityHighTriggered = false;
    humidityLowTriggered = false;
    if (((int)humidity == targetHum) {
      humidifierActive = false;
      dehumidifierActive = false;
    }
  }
  activateDevice();
  String cT = "";
  for (int i=0; i<11; i++) { cT += receivedESPChars[i]; }
  unsigned long ulCurrentTime = cT.toInt();
  // Set the local system time to the time received by the ESP01
  setTime(ulCurrentTime);
  char hourminute[6];
  sprintf(hourminute,"%02d:%02d", hour(), minute());
  lcd.setCursor(0, 0);
  lcd.print(hourminute);
  lcd.print(F("   "));
  lcd.print((int)Tf);
  lcd.print(F("F  "));
  lcd.print((int)humidity);
  lcd.print(F("%"));
  unsigned long currentMillis2 = millis();
  if ((currentMillis2 - tempHighTimer >= alarmWaitPeriod) && (acActive) && (tempHighAlarm) && (tempHighTriggered)) {
      alarmOn = true;
      lcd.setCursor(0, 1);
      lcd.print(F("Temp is too high "));
  }
  else if ((currentMillis2 - tempLowTimer >= alarmWaitPeriod) && (heaterActive) && (tempLowAlarm) && (tempLowTriggered)) {
      alarmOn = true;
      lcd.setCursor(0, 1);
      lcd.print(F("Temp is too low "));
  }
  else if ((currentMillis2 - humidityHighTimer >= alarmWaitPeriod) && (dehumidifierActive) && (humidityHighAlarm) && (humidityHighTriggered)) {
      alarmOn = true;
      lcd.setCursor(0, 1);
      lcd.print(F("Humid. too high "));
  }
  else if ((currentMillis2 - humidityLowTimer >= alarmWaitPeriod) && (humidifierActive) && (humidityLowAlarm) && (humidityLowTriggered)) {
      alarmOn = true;
      lcd.setCursor(0, 1);
      lcd.print(F("Humid. too low "));
  }
  else {
      alarmOn = false;
  }
  if (logTimer()) {  // If the logging timer is up we log
      formatData();
      printLogDataBuffer();
      logDataToMemory();
      Serial.print(F("Logged: "));
      Serial.print(ulCurrentTime);
      Serial.print(F(" "));
      Serial.print((int)Tf);
      Serial.print(F("F "));
      Serial.print((int)humidity);
      Serial.println(F("%"));
  }
  delay(500);
}


void printChipStats(boolean toesp) {
  uint32_t JEDEC = flash.getJEDECID();
  uint32_t Cap = flash.getCapacity() / 1048576;
  uint32_t result;
  char sign[6];
  if (lastKnownAddr > 1000) { result = lastKnownAddr / 1000; strcpy(sign, "KB"); }
  else if (lastKnownAddr > 1000000) { result = lastKnownAddr / 1000000; strcpy(sign, "MB"); }
  else { result = lastKnownAddr; strcpy(sign, "Bytes"); }
  if (toesp) {
    ESPserial.print(F("<Mem: "));
    ESPserial.print(result);
    ESPserial.print(F(" "));
    ESPserial.print(sign);
    ESPserial.print(F(" used of "));
    ESPserial.print(Cap);
    ESPserial.print(F(" MB>"));
  }
  else {
    Serial.println(F("Winbond chip stats"));
    Serial.print(F("JEDEC ID: "));
    Serial.println(JEDEC);
    Serial.print(F("Capacity: "));
    Serial.print(Cap);
    Serial.println(F(" MB"));
    Serial.print(F("Used: "));
    Serial.print(result);
    Serial.print(F(" "));
    Serial.print(sign);
  }
}


void formatValue(char *myvalue, char *rc, size_t size_rc) {
  myvalue[0] = '\0';
  char b[size_rc];
  for(short int i=1;i<size_rc;i++) { 
    b[i-1] = rc[i];
    if (rc[i] == '\0') {
      b[i-1] = '\0';
      break;
    }
  }
  strcat(myvalue, b);
}


void getSettings(boolean toesp) {
  char buf[SETTINGS_MEMORY_SIZE];
  char pausestate[2];
  buf[0] = '\0';
  flash.readCharArray(SETTINGS_MEMORY_ADDRESS, buf, SETTINGS_MEMORY_SIZE);
  short int s = 0;
  short int t = 0;
  for(short int i=0;i<SETTINGS_MEMORY_SIZE;i++) {
    if (s == 0) { 
      if (buf[i] == ':') { ssid[t] = '\0'; s++; t=0; }
      else { ssid[t] = buf[i]; t++; }
    }
    else if (s == 1) {
      if (buf[i] == ':') { password[t] = '\0'; s++; t=0; }
      else { password[t] = buf[i]; t++; }
    }
    else if (s == 2) {
      if (buf[i] == ':') { timezone[t] = '\0'; s++; t=0; } 
      else { timezone[t] = buf[i]; t++; }
    }
    else if (s == 3) {
      if (buf[i] == ':') { pausestate[t] = '\0'; s++; t=0; } 
      else { pausestate[t] = buf[i]; t++; }
    }
    else if (s == 4) {
      if (buf[i] == ':') { loginterval[t] = '\0'; s++; t=0; } 
      else { loginterval[t] = buf[i]; t++; }
    }
    else if (s == 5) {   
      if (buf[i] == ':') { tempTarget[t] = '\0'; s++; t=0; } 
      else { tempTarget[t] = buf[i]; t++; }
    }
    else if (s == 6) {   
      if (buf[i] == ':') { humTarget[t] = '\0'; s++; t=0; } 
      else { humTarget[t] = buf[i]; t++; }
    }
    else if (s == 7) {   
      if (buf[i] == ':') { almsettings[t] = '\0'; s++; t=0; } 
      else { almsettings[t] = buf[i]; t++; }
    }
    else if (s == 8) {   
      if (buf[i] == ':') { timer1hourON[t] = '\0'; s++; t=0; } 
      else { timer1hourON[t] = buf[i]; t++; }
    }
    else if (s == 9) {   
      if (buf[i] == ':') { timer1minuteON[t] = '\0'; s++; t=0; } 
      else { timer1minuteON[t] = buf[i]; t++; }
    }
    else if (s == 10) {   
      if (buf[i] == ':') { timer2hourON[t] = '\0'; s++; t=0; } 
      else { timer2hourON[t] = buf[i]; t++; }
    }
    else if (s == 11) {   
      if (buf[i] == ':') { timer2minuteON[t] = '\0'; s++; t=0; } 
      else { timer2minuteON[t] = buf[i]; t++; }
    }
    else if (s == 12) {   
      if (buf[i] == ':') { timer3hourON[t] = '\0'; s++; t=0; } 
      else { timer3hourON[t] = buf[i]; t++; }
    }
    else if (s == 13) {   
      if (buf[i] == ':') { timer3minuteON[t] = '\0'; s++; t=0; } 
      else { timer3minuteON[t] = buf[i]; t++; }
    }
    else if (s == 14) {   
      if (buf[i] == ':') { timer1hourOFF[t] = '\0'; s++; t=0; } 
      else { timer1hourOFF[t] = buf[i]; t++; }
    }
    else if (s == 15) {   
      if (buf[i] == ':') { timer1minuteOFF[t] = '\0'; s++; t=0; } 
      else { timer1minuteOFF[t] = buf[i]; t++; }
    }
    else if (s == 16) {   
      if (buf[i] == ':') { timer2hourOFF[t] = '\0'; s++; t=0; } 
      else { timer2hourOFF[t] = buf[i]; t++; }
    }
    else if (s == 17) {   
      if (buf[i] == ':') { timer2minuteOFF[t] = '\0'; s++; t=0; } 
      else { timer2minuteOFF[t] = buf[i]; t++; }
    }
    else if (s == 18) {   
      if (buf[i] == ':') { timer3hourOFF[t] = '\0'; s++; t=0; } 
      else { timer3hourOFF[t] = buf[i]; t++; }
    }
    else if (s == 19) {   // The ESP is all colons, the ATMEGA \0
      if (buf[i] == '\0') { timer3minuteOFF[t] = '\0'; s++; t=0; } 
      else { timer3minuteOFF[t] = buf[i]; t++; }
    }
    else { break; }
  }
  if (toesp) { 
    ESPserial.print(F("<S"));
    ESPserial.print(buf);
    ESPserial.print(F(">"));
  }
  else {
    Serial.print(F("SSID: "));
    Serial.println(ssid);
    Serial.print(F("Password: "));
    Serial.println(password);
    Serial.print(F("Timezone: "));
    Serial.println(timezone);
    Serial.print(F("Pause State: "));
    Serial.println(pausestate);
    Serial.print(F("Log interval: "));
    Serial.println(loginterval);
    Serial.print(F("Target temp: "));
    Serial.println(tempTarget); 
    Serial.print(F("Target humidity: "));
    Serial.println(humTarget); 
    Serial.print(F("Alarm settings: "));
    Serial.println(almsettings);
    Serial.print(F("Device 5 Timer On: "));
    Serial.print(timer1hourON);
    Serial.print(F(":"));
    Serial.print(timer1minuteON);
    Serial.print(F(" Off: "));
    Serial.print(timer1hourOFF);
    Serial.print(F(":"));
    Serial.println(timer1minuteOFF);
    Serial.print(F("Device 6 Timer On: "));
    Serial.print(timer2hourON);
    Serial.print(F(":"));
    Serial.print(timer2minuteON);
    Serial.print(F(" Off: "));
    Serial.print(timer2hourOFF);
    Serial.print(F(":"));
    Serial.println(timer2minuteOFF);
    Serial.print(F("Device 7 Timer On: "));
    Serial.print(timer3hourON);
    Serial.print(F(":"));
    Serial.print(timer3minuteON);
    Serial.print(F(" Off: "));
    Serial.print(timer3hourOFF);
    Serial.print(F(":"));
    Serial.print(timer3minuteOFF);
  }
  targetTemp = atoi(tempTarget);
  targetHum = atoi(humTarget);
  if (almsettings[0] == '1') { tempHighAlarm = true; }
  else { tempHighAlarm = false; }
  if (almsettings[1] == '1') { tempLowAlarm = true; }
  else { tempLowAlarm = false; }
  if (almsettings[2] == '1') { humidityHighAlarm = true; }
  else { humidityHighAlarm = false; }
  if (almsettings[3] == '1') { humidityLowAlarm = true; }
  else { humidityLowAlarm = false; }      
  if (pausestate[0] == '1') { pauseLogging = true; }
  else { pauseLogging = false; }
  unsigned long o;
  o = atoi(loginterval);
  loggingInterval = o * 1000UL;
}


void saveSettings() {
  char buf[SETTINGS_MEMORY_SIZE];
  buf[0] = '\0';
  strcat(buf, ssid);
  strcat(buf, ":");
  strcat(buf, password);
  strcat(buf, ":");
  strcat(buf, timezone);
  strcat(buf, ":");
  if (pauseLogging) { strcat(buf, "1"); }
  else { strcat(buf, "0"); }
  strcat(buf, ":");
  strcat(buf, loginterval);
  strcat(buf, ":");
  strcat(buf, tempTarget);
  strcat(buf, ":");
  strcat(buf, humTarget);
  strcat(buf, ":");
  strcat(buf, almsettings);
  strcat(buf, ":");
  strcat(buf, timer1hourON);
  strcat(buf, ":");
  strcat(buf, timer1minuteON);
  strcat(buf, ":");
  strcat(buf, timer2hourON);
  strcat(buf, ":");
  strcat(buf, timer2minuteON);
  strcat(buf, ":");
  strcat(buf, timer3hourON);
  strcat(buf, ":");
  strcat(buf, timer3minuteON);
  strcat(buf, ":");
  strcat(buf, timer1hourOFF);
  strcat(buf, ":");
  strcat(buf, timer1minuteOFF);
  strcat(buf, ":");
  strcat(buf, timer2hourOFF);
  strcat(buf, ":");
  strcat(buf, timer2minuteOFF);
  strcat(buf, ":");
  strcat(buf, timer3hourOFF);
  strcat(buf, ":");
  strcat(buf, timer3minuteOFF);
  Serial.print(F("Saving: "));
  Serial.println(buf);
  flash.eraseSector(SETTINGS_MEMORY_ADDRESS);
  flash.writeCharArray(SETTINGS_MEMORY_ADDRESS, buf, SETTINGS_MEMORY_SIZE);
}


boolean logTimer() {
  if ((pauseLogging) || (booting) || !(wificonnected)) { return false; }
  unsigned long currentMillis = millis();
  if ((currentMillis - loggingTimer >= loggingInterval) || (firsttime)) {
    loggingTimer = currentMillis;
    firsttime = false;
    return true;
  }
  else { return false; }
}


boolean sensorRequestTimer() {
  if (booting) { return false; }
  unsigned long currentMillis = millis();
  if (currentMillis - sensorTimer >= sensorInterval){
    sensorTimer = currentMillis;
    return true;
  }
  else { return false; }
}


void logDataToMemory() {
  uint32_t Myaddr = 0;
  Myaddr = flash.getAddress(sizeof(char));
  lastKnownAddr = Myaddr;
  flash.writeCharArray(Myaddr, logData, sizeof(logData));
}


void printLog(boolean toesp) {
  uint32_t paddr = 0x00; // Start at the very beginning of the chip
  if (!(toesp)) { Serial.println(F("____Log_Data____")); }
  else { ESPserial.print(F("<")); }
  while(1) {
    if (endOfData(paddr)) { break; }
    flash.readCharArray(paddr, logData, sizeof(logData));
    paddr += LOG_DATA_SIZE;
    if (toesp) {
      for(uint32_t i=0; i<sizeof(logData); i++) { ESPserial.print(logData[i]); }
      if (endOfData(paddr)) { ESPserial.print("z"); }
      else { ESPserial.print("n"); }
    }
    else { Serial.println(logData); }
    delay(3);
  }
  if (!(toesp)) { Serial.println(F("____End____")); }
  else { ESPserial.print(">"); }
}
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

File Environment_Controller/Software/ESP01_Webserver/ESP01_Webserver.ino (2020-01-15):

#include <ESP8266WiFi.h>
#include <WiFiClient.h>
#include <ESP8266WebServer.h>
#include <ESP8266mDNS.h>
#include <time.h>
#include <TimeLib.h>
#include <avr/pgmspace.h>
#if !defined(__time_t_defined) // avoid conflict with newlib or other posix libc
typedef int time_t;
#endif
#define timezoneEepromAddr 0
#define ssidEepromAddr 10
#define passwordEepromAddr 40
#define SSID_SIZE 25
#define PASSWORD_SIZE 25

//   USED TO DEBUG MEMORY PROBLEMS
//   REPORTS AVAILABLE MEMORY LEFT IN THE HEAP
extern "C" {
#include "user_interface.h"
}
void freeMemory() {
  Serial.print(F("< bytes left: "));
  Serial.print(system_get_free_heap_size());
  Serial.print(F(">"));
}

ESP8266WebServer server (80); // Start up the web server
ESP8266WebServer APserver (81);

int timezone = 0;
const byte numChars = 128;
char receivedChars[numChars]; // an array to store the received data
char myPassword[PASSWORD_SIZE];
char ssid[SSID_SIZE];
char interval[6];
int iplen = 16; // Length of the IP address string
char ip[17]; // The IP address
char tempTarget[3];
char humTarget[3];
char alarmstate[5];
char timer1hourON[3];
char timer1minuteON[3];
char timer2hourON[3];
char timer2minuteON[3];
char timer3hourON[3];
char timer3minuteON[3];
char timer1hourOFF[3];
char timer1minuteOFF[3];
char timer2hourOFF[3];
char timer2minuteOFF[3];
char timer3hourOFF[3];
char timer3minuteOFF[3];
String temp = ""; // for storing the temperature and humidity data
String humidity = "";
int devices[8]; // Stores the off/on state of all 8 devices
boolean humidityHighAlarm = false, humidityLowAlarm = false, tempHighAlarm = false, tempLowAlarm = false;
boolean newData = false, dataErr = false, waitForData = false, recvInProgress = false, logPaused = false, haveSettings = false, triedServer = false;


// function prototypes
void parseSettings();
void startPage();
void middlePage(const __FlashStringHelper*);
void endPage();
void ajaxReply(const __FlashStringHelper*);
void ajaxReply(char&); // Overloaded function
void returnFail(const __FlashStringHelper* );
void scanAllNetworks();
boolean handleTimeout(const __FlashStringHelper*, boolean);
void handleSubmit();
void handleRoot();
void handleAPSubmit();
void handleAPRoot();
void handleNotFound();
void recvData();
void startAP();
boolean startServer();
void assignDev();
void fetchAlarmSettings();


const char ap_welcome[] PROGMEM = R"rawliteral(
<!DOCTYPE HTML><html><head><title>Seni-Pot Sensor and Device Hub</title><meta charset="utf-8"><meta name="viewport" content="width=device-width, initial-scale=1, shrink-to-fit=no"><style>.form-style-6{font:95%Arial,Helvetica,sans-serif;max-width:400px;margin:10px auto;padding:16px;background:#F7F7F7}.form-style-6 h1{background:#5bc0de;padding:20px 0;font-size:140%;font-weight:300;text-align:center;color:#fff;margin:-16px-16px 16px-16px}.form-style-6 input[type="text"]
{-webkit-transition:all 0.30s ease-in-out;-moz-transition:all 0.30s ease-in-out;-ms-transition:all 0.30s ease-in-out;-o-transition:all 0.30s ease-in-out;outline:none;box-sizing:border-box;-webkit-box-sizing:border-box;-moz-box-sizing:border-box;width:100%;background:#fff;margin-bottom:4%;border:1px solid #ccc;padding:3%;color:#555;font:95%Arial,Helvetica,sans-serif}.form-style-6 input[type="text"]:focus
{box-shadow:0 0 5px #52aac4;padding:3%;border:1px solid #52aac4}.form-style-6 input[type="submit"],.form-style-6 input[type="button"]{box-sizing:border-box;-webkit-box-sizing:border-box;-moz-box-sizing:border-box;width:100%;padding:3%;background:#5bc0de;border-bottom:2px solid #499eb8;border-top-style:none;border-right-style:none;border-left-style:none;color:#fff}.form-style-6 input[type="submit"]:hover,.form-style-6 input[type="button"]:hover{background:#52aac4}</style></head><body><div class="form-style-6"><h1>Welcome!</h1>Please enter your router's SSID and password for Internet connection.<br><br><form action="http://192.168.4.1:81" method="POST"><input name="ARG" type="text" placeholder="SSID"><input name="ARG1" type="text" placeholder="Password"><input type="submit" value="submit"></form></div></body></html>
)rawliteral";


const char ap_thankyou[] PROGMEM = R"rawliteral(
<!DOCTYPE HTML><html><head><title>Seni-Pot Environment Controller</title><meta charset="utf-8"><meta name="viewport" content="width=device-width, initial-scale=1, shrink-to-fit=no"><style>.form-style-6{font:95%Arial,Helvetica,sans-serif;max-width:400px;margin:10px auto;padding:16px;background:#F7F7F7}.form-style-6 h1{background:#43D1AF;padding:20px 0;font-size:140%;font-weight:300;text-align:center;color:#fff;margin:-16px-16px 16px-16px}</style><script language="javascript">var ajaxRequest=null;var ajaxResult=null;var count=15;var attempts=0;if(window.XMLHttpRequest){ajaxRequest=new XMLHttpRequest()}
else{ajaxRequest=new ActiveXObject("Microsoft.XMLHTTP")}
function ajaxLoad(ajaxURL){if(!ajaxRequest){alert("AJAX is not supported.");return}
ajaxRequest.open("GET",ajaxURL,!0);ajaxRequest.onreadystatechange=function(){if(ajaxRequest.readyState==4&&ajaxRequest.status==200){document.getElementById("msg").innerHTML=ajaxRequest.responseText}}
ajaxRequest.send()}
var si=setInterval(function(){if(attempts>2){document.getElementById("msg").innerHTML="It seems the WiFi connection could not be established. Please click back and try again."}
else if(document.getElementById("counter")){document.getElementById("counter").innerHTML=count;count--;if(count<1){ajaxLoad("http://192.168.4.1:81?ARG=getipaddress");count=15;attempts++}}
else{clearInterval(si)}},1000);</script></head><body><div class="form-style-6"><h1>Thank you!</h1><h3 id="msg">Please wait for this page to automatically reload in&nbsp;<span id="counter"></span>&nbsp;seconds with the IP address you will need to access this device on your router.</h3></div></body></html>
)rawliteral";
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

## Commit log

2019-02-07 Updated arduino code with comments and put the files into appropriate folders.
2019-02-08 Added BOM file
    [Environment_Controller_BOM.csv]
2019-02-08 Added schematic jpg
2019-02-15 Uncommented critical lines of code. Updated the logging timer to log only every 5 minutes although it still checks temp and humidity every 15 seconds and activates devices based on that.
2019-02-19 Added software for soil sensor
    This software is based on i2c communication. The pcb for this setup was already ordered when I decided that the spi standard is a much better way to go. So this version will be updated very shortly after I design a new pcb.
2019-04-12 Rough draft prototype schematics
2019-04-12 schematic added for soil sensor
2019-09-20 New software for new boards.
2020-01-15 Upgrade to 2.0
    Here we go Woo hoo!
    [Environment_Controller_BOM.csv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]
